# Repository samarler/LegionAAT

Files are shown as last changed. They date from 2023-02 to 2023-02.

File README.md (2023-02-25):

# LegionAAT

Star Wars Legion ATT Lighted and Motorized Modification

Modify a Star Wars Legion ATT to motorize the main turret and side weapons which are controled by a remote controller conneceted over BTLE. 
The ATT is uses an Adafruit Feather 32u4 Bluefruit to recieve and execute commands.

Included in this repository are stl files for printing out parts needed to complete the modification, code for the Adafruit Feather 32u4 Bluefruit and a draft set of instructions on how to complete the modification (see instructions for BOM).

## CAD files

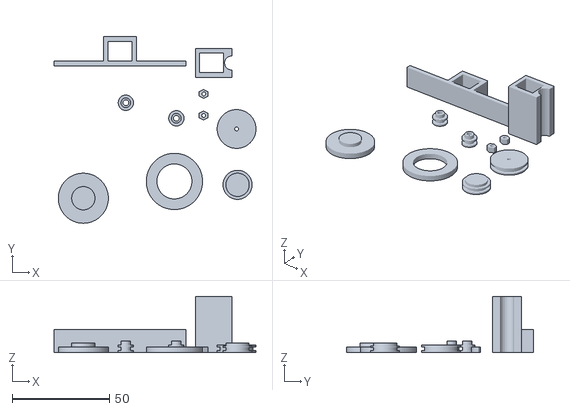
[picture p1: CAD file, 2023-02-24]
AAT Modification Parts.stl
104.0 x 96.1 x 28.9

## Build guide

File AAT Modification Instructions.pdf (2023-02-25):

# Star Wars Legion AAT Modification Instructions

## Overview

These instructions are for modifying a Star Wars Legion AAT Federation Battle Tank to add a rotating turret, movable side guns and LEDs in the launch tubes. Control for these modifications are current supported by using a free phone app (available for the iPhone or Android) provided but Adafruit. It is assumed you have soldering and basic electronics experience.

The instructions are presented din the following sections and should be followed as presented:
1. Turret Modifications
2. Side Gun Modifications
3. Upper Body Assembly
4. Lower Body Modifications
5. Electronics Assembly
6. Final Assembly
7. Operation

To complete this project you will need the schematic for electronic component assembly, the additional parts from the STL files and the parts listed in the Build of Materials (BOM).

BOM
Qty | Part

1 AAT Model

2 N20 3v 30 rpm DC Motors

1 Dual Motor Control Board

1 Adafruit Feather 32u4 Bluefruit LE

1 Adafruit Lithium Ion Polymer Battery 3.7v 1200mAh

6 Amber 3v 3mm LEDs

6 47 OHM Resistor

1 Sealed Bearing 18mm x1 2mm
1 Music Wire .062 (1.57mm) in Diameter 1 Two pole sliding switch

## Section 1 Turret Modifications

The following parts from the base kit will be needed for this step:
- Bottom Turret Piece
- Left Half of Upper Body

In addition you will need the following parts from the BOM and from the provided STL files (See photo on right for part identification):
- Sealed Bearring
- Drive Pulley
- Turret Ring
- Turret Mount

### Step 1 Turret Assembly Preparation

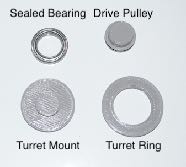
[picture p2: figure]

Modify the bottom turret piece by removing the lip where it connects to the body (See before and after photos below).

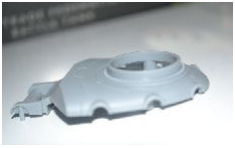
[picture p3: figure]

### Step 2 Turret Modifications Assembly

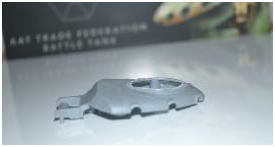
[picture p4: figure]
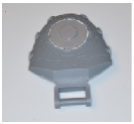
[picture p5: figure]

Glue the turret mount to the bottom turret piece as shown.

Before | After

Glue the bottom piece of the turret ring to the body of the AAT as shown (only glue to the right side, wait until final body assembly to glue the left side).

Insert the sealed bearing into the turret ring and the drive pulley into the turret ring as shown.Attach the bottom piece of the turret to the body of the AAT by press fitting the the turret mount into the sealed bearing. The turret should spin around with little effort.

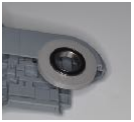
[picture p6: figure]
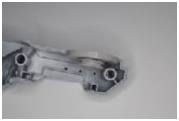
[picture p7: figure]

## Section 2 Side Gun Modifications

The following parts from the base kit will be needed for this step:
- Left and Right Halves of Upper Body
- Left and Right Side Gun Mounts

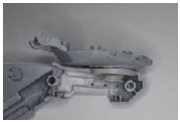
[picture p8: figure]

In addition you will need the following parts from the BOM and from the provided STL files (See photo on right for part identification):
- Side gun music wire mounts
- Side gun motor mount
- Side gun music wire pulley
- Turret motor pulley
- Drive bands for the side guns and turret
•

Complete the side gun modifications and partial assembly using the following steps.

### Step 1 Side Gun Mount Modifications

Complete the following for each of the two gun mounts. Modify the inside of the mount by removing the posts used to assist in assembly and cutting a hole in the end that will align with the previously created hole as shown (unmodified parts shown for comparison). Glue the two sides together making sure they are properly aligned. Clip the tips off of the end and then use a 2.5mm pin vise bit to create a hole in the end as shown.

Use a 3mm pin vise to create a hole in the upper body side that aligns with the holes in the gun mount as shown.

Prepare the side guns for mounting by inserting the axel mounts as shown.

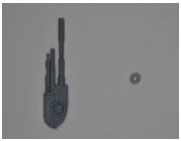
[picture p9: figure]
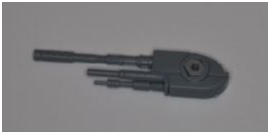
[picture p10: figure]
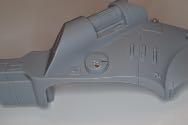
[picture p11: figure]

Drill holes in the body sides as shown and attach the side gun mounts.

Press fit a small pulley onto one of the motors and insert into the side gun motor mount. Glue this assembly to a body support as shown.

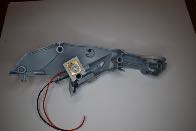
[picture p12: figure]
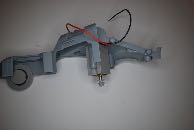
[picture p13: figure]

### Step 2 Assemble and Connect Side Guns

Start assembly of side gun system by gluing the music wire into one of the side guns. Insert the side gun assembly into the gun mount and slide the drive pulley onto music wire and add a drive band around the assembly. Test fit the wire by assembling the body and inserting the wire into the modified gun mounts and make sure it can freely spin. Make any additional modifications, such as widening holes, as needed.

### Step 3 Complete upper body assembly

Prepare for assembly by adding a drive band on the turret pulley and wrapping the other end around the gun mount. Assemble the two body sides (body sides only, do not assemble the body parts under the turret or under the motors) with the turret motor mount in-between the two body parts.

Press fit a small drive pulley onto the turret motor and insert motor into it’s mount from the bottom, checking to make sure it does not extend too high for the top cover piece to fit. Insert the music wire with the side gun mounted through the gun mount, then through the drive pulley while adding the drive band and then through the opposite gun mount. Attach the drive bands to their respective motor.

## Section 4 Lower Body Modifications

Using 3mm drill bit, drill out the center of the launch tubes and a hole in the center rear as shown below:

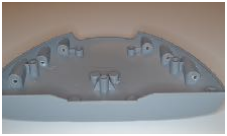
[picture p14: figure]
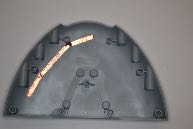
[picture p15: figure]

Using copper tape (available in hobby shops in the stained glass section) to create a bus that will be used as the common ground as shown.

## Section 5 Electronics Assembly

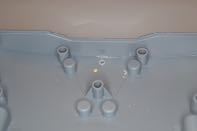
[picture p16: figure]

The following items from the BOM will be needed for this section:

- Adafruit Feather 32u4 Bluefruit LE
- Motor Controller Breakout Board
- Adafruit Lithium Ion Polymer Battery 3.7v 1200mAh

- Six 3v 3mm Amber LEDs
- Six 47ohm Resisters
- Two pole sliding switch

In addition you’ll need hook up wire. Before beginning these steps, place the 32u4 Bluefruit LE, motor controller and battery in their final locations but do not secure them to the lower body top at this time.

### Step 1 Controller Preparation

Using your method of choice, flash the provided code to the Adafruit Feather 32u4 Bluefruit LE. (See https://learn.adafruit.com/adafruit-feather-32u4-bluefruit-le/setup for instructions on setting up and using the Arduino IDE and installing the BLE Libraries needed.) Solder hook up wires between the Adafruit Feather 32u4 Bluefruit LE and motor controller breakout board. Pre-measure the wire length by placing the Feather and the motor controller board in the lower body top. Pull the motor wires through the hole previously made and connect to the motor controller breakout board. Solder 47 ohm resisters into pins A0-A5, with hook up wire on the ends. Use heat shrink tubing to reenforce the connections. Solder hookup wires to the Adafruit GND and motor controller breakout board PWR- for later connectivity to the ground bus. Using hookup wire, solder one pole of the sliding switch to the pin labeled EN on the Adafruit Feather 32u4 Bluefruit LE and another to the ground bus. Install the switch in the hole previously prepared. See tables for proper connections.

When completed it should look similar to this photo.

Feather | Controller
3V3 | PWR+
12 | IN1
11 | IN2
6 | IN3
5 | IN4 | A4 | LED5
| | A5 | LED6
Feather | LED
A0 | LED1
A1 | LED2
A2 | LED3
A3 | LED4
Motor | Controller
Turret Motor + | Motor A +
Turret Motor - | Motor A -
Side Gun Motor + | Motor B +
Side Gun Motor - | Motor B -

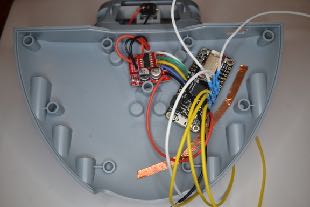
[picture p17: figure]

### Step 2 Prepare and Install LEDs

For each of the six LEDs, solder one of the hookup wires on the Adafruit Feather to the anode (positive) wire on the LED. Solder a hookup wire to the cathode (negative) wire and solder the other end to the ground bus. Insert each LED into a launch tube.

### Step 3 Mount Components

Secure the 32u45 Bluefruit LE, motor breakout board and battery to the lower body top using double sided tape, placing them as shown.

## Section 6 Final Assembly

Follow the instructions provided in the kit to complete the assembly of the model. You may want to modify the parts that go under the turret and under and over the motors for future access in case there is a problem with the drive belts.

## Section 7 Operation

Download the Adafruit Bluefruit LE Connect app for iOS from the Apple App Store or for the Android from the Google Play Store. Download the instructions on how to use the app from www.adafruit.com (https://cdn-learn.adafruit.com/downloads/pdf/bluefruit-le-connect.pdf). The sections of interest are Scan for Devices and Controller. You will use the Controller Pad found in the Controller section to control the AAT. See the diagram below for control pad commands.

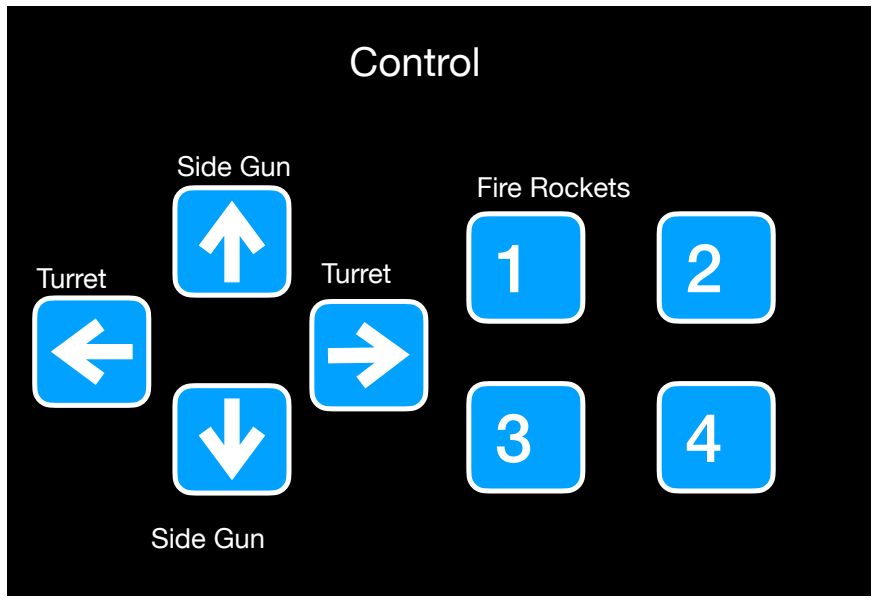
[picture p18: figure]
Turret; Side Gun; Fire Rockets; Control

Turret Left

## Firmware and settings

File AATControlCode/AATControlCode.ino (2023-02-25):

/*****************************************************************************
 Version 0.2.24.23

 Code is written for the Adafruit Feather 32u4 Bluefruit LE and includes Adafruit Bluetooth libraries.
 
 This code is for a modified Star Wars Legion AAT to motorize the turret, side guns and LEDs in the
 missle slots. Control the AAT using AdaFruit Bluefruit LE Connect from an iOS or Android devices. 
 Once connected to the ATT, select Controller -> Control Pad. The up and down arrows control the side
 guns, the left and right arrows control the turret and the 1 button controls the LEDs.

 Written by Scott Marler. GNU General Public License v3.0, check license.txt
 for more information.
 **************************************************************************/

//Libraries
#include <string.h>
#include <Arduino.h>
#include <SPI.h>
#include "Adafruit_BLE.h"
#include "Adafruit_BluefruitLE_SPI.h"
#include "Adafruit_BluefruitLE_UART.h"
//Configuration file for Bluetooth 
#include "BluefruitConfig.h"
//Constants used in the code
#define FACTORYRESET_ENABLE         0
#define MINIMUM_FIRMWARE_VERSION    "0.6.6"
#define MODE_LED_BEHAVIOUR          "MODE"
#define TPIN1 11
#define TPIN2 12
#define GPIN1 6
#define GPIN2 5
#define LED1 A0
#define LED2 A1
#define LED3 A2
#define LED4 A3
#define LED5 A4
#define LED6 A5
//Array used for LEDs
int leds[10] = {LED1,LED2,LED3,LED4,LED5,LED6};
//Setup Bluetooth
Adafruit_BluefruitLE_SPI ble(BLUEFRUIT_SPI_CS, BLUEFRUIT_SPI_IRQ, BLUEFRUIT_SPI_RST);

// A small helper
void error(const __FlashStringHelper*err) {
  Serial.println(err);
  while (1);
}

// function prototypes over in packetparser.cpp
uint8_t readPacket(Adafruit_BLE *ble, uint16_t timeout);
float parsefloat(uint8_t *buffer);
void printHex(const uint8_t * data, const uint32_t numBytes);

extern uint8_t packetbuffer[];

//Setup
void setup(void) {
  delay(500);
  Serial.begin(115200);
  randomSeed(analogRead(0));
//Setup GPIO pins for thier use
  pinMode(GPIN1,OUTPUT);
  pinMode(GPIN2,OUTPUT);
  pinMode(TPIN1,OUTPUT);
  pinMode(TPIN2,OUTPUT);
  pinMode(LED1,OUTPUT);
  pinMode(LED2,OUTPUT);
  pinMode(LED3,OUTPUT);
  pinMode(LED4,OUTPUT);
  pinMode(LED5,OUTPUT);
  pinMode(LED6,OUTPUT);
  delay(100);
  
  /* Initialise the Bluetooth module */
  Serial.print(F("Initializing Bluetooth "));

  if ( !ble.begin(VERBOSE_MODE) ){
    error(F("Couldn't find Bluetooth interface."));
  }
  Serial.println( F("OK!") );

  if ( FACTORYRESET_ENABLE ) {
    /* Perform a factory reset to make sure everything is in a known state */
    Serial.println(F("Performing a factory reset: "));
    if ( ! ble.factoryReset() ){
      error(F("Couldn't factory reset"));
    }
  }

  /* Disable command echo from Bluefruit */
  ble.echo(false);

   // Change device name advertized for Bluetooth
  Serial.println(F("Change Name to AAT"));
  if(!ble.sendCommandCheckOK(F("AT+GAPDEVNAME=AAT"))) {
    Serial.println(F("Failed to change name"));}
  else {Serial.println(F("Name Changed"));}

  Serial.println("Requesting Bluetooth info:");
  /* Print Bluefruit information */
  ble.info();

  Serial.println(F("Ready for controller connection"));
  Serial.println();

  ble.verbose(false);  // debug info is a little annoying after this point!

  /* Wait for connection */
  while (! ble.isConnected()) {
      delay(500);
  }

  // LED Activity command is only supported from 0.6.6
  if ( ble.isVersionAtLeast(MINIMUM_FIRMWARE_VERSION) ) {
    // Change Mode LED Activity
    Serial.println(F("******************************"));
    Serial.println(F("Change LED activity to " MODE_LED_BEHAVIOUR));
    ble.sendCommandCheckOK("AT+HWModeLED=" MODE_LED_BEHAVIOUR);
    Serial.println(F("******************************"));
  }
  Serial.println( F("Switching to DATA mode."));
  ble.setMode(BLUEFRUIT_MODE_DATA);
}

//Main loop
void loop(void) {
  // Wait for packet

  uint8_t len = readPacket(&ble, BLE_READPACKET_TIMEOUT);
  if (len == 0) return;

  // When button pushed perform operation requested
  if (packetbuffer[1] == 'B') {
    uint8_t buttnum = packetbuffer[2] - '0';
    boolean pressed = packetbuffer[3] - '0';

    if(pressed) {
      switch(buttnum) {
        case 1:
          fire();
          break;
        case 5:
          digitalWrite(GPIN1,HIGH);
          break;
        case 6:
          digitalWrite(GPIN2,HIGH);
          break;
        case 7:
          digitalWrite(TPIN2, HIGH);
          break;
        case 8:
          digitalWrite(TPIN1,HIGH);
          break;

        default:
          stopAllMotors();
          break;
      }
    } else {
      stopAllMotors();
    }

    Serial.print ("Button "); Serial.print(buttnum);
    if (pressed) {
      Serial.println(" pressed");
    } else {
      Serial.println(" released");
    }
  }
}

//Function to stop all motors
void stopAllMotors() {
  digitalWrite(GPIN1,LOW);
  digitalWrite(GPIN2,LOW);
  digitalWrite(TPIN1,LOW);
  digitalWrite(TPIN2,LOW);
}

//Function to simulate missle fire
int fire() {
  boolean c = true;
  int n = 0;
  int l[10];
  for(int i=0;i<10;i++) {
    l[i]=0;
  }
  while(n < 9) {
    int t = random(0,10);
    for(int x=0;x<10;x++) {
      if(t == l[x]) {c = false;break;}
    }
    if(c) {l[n] = t;n++;}
    c = true;
  }
  for(int i=0;i<10;i++) {
    digitalWrite(leds[l[i]],HIGH);
    delay(100);
    digitalWrite(leds[l[i]],LOW);
  }
}

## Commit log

2022-11-14 Update README.md
    Added BOM
2022-11-14 Update README.md
    Updated BOM
2022-12-08 Add files via upload
    New turret ring design.
    [TurretRing.stl]
2023-02-25 Add files via upload
    Updated pin assignments
2023-02-25 Add files via upload
    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
